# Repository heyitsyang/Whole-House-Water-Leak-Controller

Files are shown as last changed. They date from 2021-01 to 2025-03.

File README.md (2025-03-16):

# **Whole House Water Leak Detection & Valve Control**
The project described here is a part of a complete water detection system consisting of the following major components:
- Water Valve to cut off water flow should a leak be detected
- Pressure Sensor to detect small or slow leaks using a periodic static pressure test (weeping valves, toilet internals, etc.)
- Supervisory computer to schedule tests, analyze results, respond to leaks, and provide a UI.  I use Home Assistant, but a similar MQTT capable system should suffice.
- Remote water leak sensors placed under sinks and other areas of likely leakage to trigger immediate water cutoff for sudden leaks

The project detailed here satisfies the first two components in the list above.  A robust MQTT command set is incorporated for interfacing to a supervisory computer.

The code provided does not require the pressure sensor or the valve to be installed to be useful.  It is possible to use the system as a valve control box only or a pressure sensor only.
<br/><br/>
## **Pressure sensor**
If you need only valve control, the pressure sensor does not have to be installed. Just be sure to set the software accordingly either by setting the *#define INITIAL_PRESSURE_SENSOR_INSTALLED_STATE* directive in the code or during runtime using the *pressureInstalled* MQTT command.

The pressure sensor used is a M3200 series I2C interfaced model from TE Connectivity Industrial Pressure Sensors.  The specific model I used is M32JM-000105-100PG purchased from Mouser Electronics.  If you use this model be aware that external 4.7K pull up resistors are required for the SDA and SCL wires.

### **Pressure Sensor Default Programming**
Programming behavior can be changed by varying the *#define* directives in the program.  Here is the default behavior:
- Sensor is read every 500ms
- Under quiescent conditions, pressure is published every 5 minutes
- If there is a pressure change of more than 0.3 PSI, the current pressure is published every five seconds
- If the pressure sensor cannot be read a fault will be published every 5 minutes
<br/><br/>
## **Motorized Valve**
If you need only pressure sensing, the valve does not have to be installed.  Just be sure to set the software accordingly either by setting the *#define INITIAL_VALVE_INSTALLED_STATE* directive in the code or during runtime using the *valveInstalled* MQTT command.

The motorized valve used is a U.S. Solid model JFMSV00014 3/4" diameter Motorized Ball Valve (available on Amazon).  _Be sure you order the diameter approriate for your plumbing_.  

This model has five wires - two to control the valve (via polarity reversal) and three to connected to open/closed indicator switches.  There are other models from U.S. Solid that look the same but have different wire configurations.  The five-wire model is required if you wish to use this code without modification.

The five-wire model enables detection of the valve state.  Since there is a manual switch for opening/closing the valve, there is a possibilty that the last stored state of the valve in software is out of sync with the actual valve position.  The software compensates for this by sychronizing with the actual state of the valve.
<br/><br/>
## **Software**
The Water Main Controller software is written using PlatformIO.  However, it can be compiled using Arduino IDE by simply copying the text in src/main.cpp to a Arduino sketch file (e.g watermain.ino) and compiling using the IDE.  You will need to add the libraries indicated in the code comments before compiling.

### **Libraries**
Two libraries must be added to the development environment to sucessfully compile.  They are available via the Arduino or PlatformIO library manager or from github:
- knolleary/PuSubClient
- ropg/ezTime

### **MQTT**
All reporting and interaction with The Water Main Montior is accomplished via MQTT.  If you've never heard of MQTT, there are many good tutorials on the web,  It is best to have a firm grasp on MQTT concepts before beginning this project.

Although there is robust logging available from the serial port, the primary interface for interaction and configuration is through MQTT reports and commands.  The documentation for commands are in the code and are purposely not duplicated here to avoid having to maintain documentation in multiple places.

Using a MQTT tool such as MQTT Explorer (http://mqtt-explorer.com/) is strongly recommended to fully understand, configure, test, and debug the project.

### **Static Pressure Test**
Both the pressure sensor and the valve must be installed to use this feature.  

A Static Pressure Test is used to check for small leaks by turning off the water coming into the house for a short time and watching for a pressure drop when water is not being used and the hot water heater is not heating.  Determining hot water heater activity requires an additional sensor that is outside the scope of this project.  Short of sensing hot water heater activity, simply pick a time for the test when the hot water heater activity is unlikely.

The amount of pressure drop indicating a leak will vary with the plumbing system.  You will need to establish what pressure drop is normal for your properly sealed plumbing system in order to determine the setting for your leak alarm threshold.

A Static Pressure Test is initiated by sending the *sptStartTest* MQTT command (read code comments for all commands) to the controller.  Once the command is received, the test begins immediately.  

Results are published via MQTT at the end of the test.  It is up to program logic in the supervisory computer to determine if the test passed, failed, or is invalid due to water use or hot water heater activity.  In my case the program logic is accomplished using Home Assistant.
- Default SPT duration is 10 minutes
- Pressure reporting frequency is set to every 30 seconds during SPT.  Reporting frequency is restored to pre-test frequency when the test concludes.
- Valve is closed at the start and restored to pre-test state at end of test
- Timestamp of start of test, test duration, beginning pressure, ending pressure, and the difference is published via MQTT at the *end* of the test
- If a sudden/large pressure drop occurs during the SPT, the test a aborted, the valve is opened, and an aborted SPT status is published .  This avoids the inconvenience of water not being availble for the duration of the SPT test.  The supervisory computer can reschedule a test should this occur.

### **Home Assistant**
If you use Home Assistant, the following are the MQTT definitions required for your configuration.yaml.  You will need to study the MQTT commands and topics in the code to write your own data display, leak actions & alarms, etc.

Obviously, if you did not install both pressure sensor and valve, the Static Pressure Test and some parts of the MQTT configuration will not apply.

```
 mqtt:
    sensor:
      - unique_id: water_spt_data_status
        name: "SPT Data Status"
        state_topic: "watermain/spt_data_status"
        json_attributes_topic: "watermain/data_status/attributes"
        qos: 0

      - unique_id: water_pressure
        name: "Water Pressure"
        state_topic: "watermain/water_pressure"
        qos: 0
        device_class: "pressure"
        unit_of_measurement: "psi"
        expire_after: 600 # state becomes "unknown" after 10 minutes

      - unique_id: water_temperature
        name: "Water Temperature"
        state_topic: "watermain/water_temperature"
        qos: 0
        device_class: "temperature"
        unit_of_measurement: "°F"
        expire_after: 600 # state becomes "unknown" after 10 minutes

      - unique_id: unvalidated_water_static_pressure_test_result # see sensor.validated_water_static_pressure_test_result
        name: "Unvalidated Water Static Pressure Test Result"
        state_topic: "watermain/spt_result"
        unit_of_measurement: "psi"
        json_attributes_topic: "watermain/spt_result/attributes"

    switch:
      - name: "Water Valve"
        unique_id: water_valve
        state_topic: "watermain/valve_zeroisclosed"
        command_topic: "watermain/cmd/valveState"
        payload_on: "1"
        payload_off: "0"
        qos: 2
```
<br/>
The following are the template sensors derived from the the controller data.
<br/>

```
sensor:
    - platform: template
      sensors:
        last_static_pressure_test:
          friendly_name: "Last Static Pressure Test"
          value_template: >-
            {{ as_timestamp( state_attr('sensor.unvalidated_water_static_pressure_test_result', 'test_end'), '' ) 
            | timestamp_custom ('%m/%d %H:%M', True, 'unknown') }}

    - platform: template
      sensors:
        validated_water_static_pressure_test_result:
          friendly_name: "Validated Water Static Pressure Test Result"
          unit_of_measurement: "psi"
          value_template: >-
            {% if (is_state('sensor.spt_data_status', 'valid')) %}
              {{ states('sensor.unvalidated_water_static_pressure_test_result') }}
            {% endif %}

    - platform: template
      sensors:
        water_static_pressure_loss_per_minute:
          friendly_name: "Pressure Loss per Minute"
          unit_of_measurement: "psi"
          value_template: >
            {{ (states('sensor.validated_water_static_pressure_test_result') | float(default=0)) / 
              (states('input_number.inp_num_spt_duration') | float(default=0)) }}

    - platform: template
      sensors:
        min_water_pressure:
          friendly_name: "Min Water Pressure"
          unit_of_measurement: "psi"
          value_template: "{{ state_attr('sensor.24hr_avg_water_pressure', 'min_value') }}"

    - platform: template
      sensors:
        max_water_pressure:
          friendly_name: "Max Water Pressure"
          unit_of_measurement: "psi"
          value_template: "{{ state_attr('sensor.24hr_avg_water_pressure', 'max_value') }}"      
```
<br/>
To manually start the SPT test, use the following script.
<br/>

```
script:
  scr_manual_spt:
    sequence:
    - service: mqtt.publish
        data:
        topic: watermain/cmd/sptStart
```
For a more comprehensive example or more details, my complete Home Assistant code is available at https://github.com/yang3535/HomeAssistantConfigUnderHassOS.  Look in the following files and search for "spt" to see how I implemented various functions.
- automations/automations.yaml
- sensors.yaml
- scripts.yaml

<br/><br/>
Below is my Home Assistant dashboard for configuring & monitoring the system.  Note the water heater sensor shown in the dashboard is not part of this project.  Since the water heater being active influences the SPT results, I postpone the SPT test in my automation if the water heater is active.  If you run the Static Pressure Test in the middle of the night, water heater interference is less likely, so water heater sensor is optional.

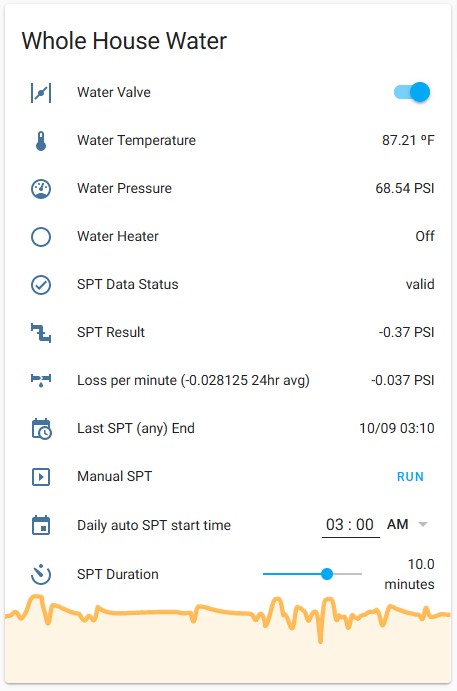
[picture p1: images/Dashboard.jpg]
Dashboard


<br/><br/>
## **Electronics**
The list of components I used is below.  It looks like a long list because of the URLs, but here are only eight main items.  If you plan to 3D print the enclosure, buying the specific electronic parts below will ensure fit inside the enclosure.

- Qty 1 - M32JM-000105-100PG - 
TE Connectivity Industrial Pressure Sensor part no. 20006465-00
 (Mouser Electronics part # 824-M32JM-000105-100) https://www.mouser.com/ProductDetail/Measurement-Specialties/M32JM-000105-100PG/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
- Qty 1 (optional)  - Motorized Ball Valve model JFMSV00014- .75" Stainless Steel Electrical Ball Valve with Full Port, 9-24V DC and 5 Wire Setup, can be used with Indicator Lights, [Indicate Open or Closed Position] by U.S. Solid
https://amazon.com/dp/B06Y11B8VN/ref=cm_sw_em_r_mt_dp_zI.YFbWGFTD1B?_encoding=UTF8&th=1
- Qty 1 - WeMos ESP8266 D1 Mini https://www.amazon.com/Makerfocus-NodeMcu-Development-ESP8266-Compatible/dp/B01N3P763C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
- Qty 1 - mxuteuk 3pcs/pkg (only one is needed) Momentary Rocker Switch Toggle Power Button (ON)/Off/(ON) 6 Pin 250V/10A 125V/15A, Use for Car Auto Boat Household Appliances KCD2-223-JT  by mxuteuk https://amazon.com/dp/B0885W19KL/ref=cm_sw_em_r_mt_dp_.A.YFbV7YQZZY?_encoding=UTF8&psc=1
- Qty 1 - Electronics-Salon 2 DPDT Signal Relay Module Board, DC 5V Version, for Arduino Raspberry-Pi 8051 PIC.  by Electronics-Salon.  https://www.amazon.com/Electronics-Salon-Signal-Version-Arduino-Raspberry-Pi/dp/B00SKG6OM4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
- Qty 1 - RGB LED https://www.amazon.com/Diffused-Multicolor-Common-Cathode-Arduino/dp/B01FDD3B72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
- Qty 1 - LM2596 Buck Converter https://www.amazon.com/DZS-Elec-Adjustable-Electronic-Stabilizer/dp/B06XRN7NFQ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
- Qty 1 - 12VDC Power supply 
https://amazon.com/gp/product/B07HNV6SBJ/ref=ppx_yo_dt_b_asin_title_o01_s00?ie=UTF8&psc=1

The panel mount holes of the 3D printed enclosure accomodates the specific connectors listed below.  If you don't want to use these connectors, the 3D Fusion360 source file can be modified to suit whatever connectors you choose.

Note the aviation connectors below are specified with different number of pins to prevent accidentally interchanging the pressure sensor and the valve control wires.  It is possible to use the 6-pin version for both wires if you don't confuse the two or select pin connections so no harm is done if interchanged.  

- Qty 1 - Female DC Power Jack Panel Mount 5.5mm x 2.1mm https://www.amazon.com/TOTOT-5-5mm-Female-Socket-Electrical/dp/B077YB75N3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
- Qty 1 - 4-pin Aviation Connector set https://amazon.com/gp/product/B07GZFQDNS/ref=ppx_yo_dt_b_search_asin_title?ie=UTF8&psc=1
- Qty 1 - 6-pin Aviation Connector set https://smile.amazon.com/gp/product/B07L1Q69R5/ref=ppx_yo_dt_b_search_asin_title?ie=UTF8&psc=1
<br/><br/>
### Wiring & Assembly

Wiring Diagram - The Wemos D1 Mini ESP8266 device is shown right side up in the diagram below for clarity, but will actually be mounted upside down in the 3D printed enclosure.

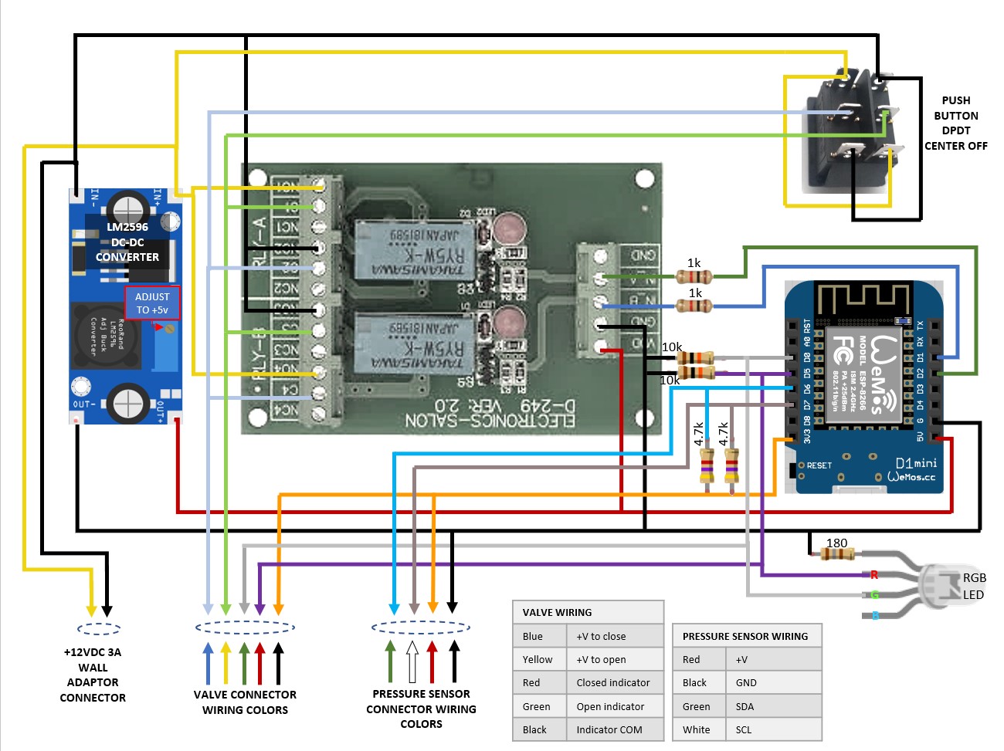
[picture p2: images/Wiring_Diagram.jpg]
Circuit Diagram

<br/><br/> 

Components mounted in 3D printed case - Note the color of wires do not match those of the above diagram.  The indicator LED is mounted above the manual valve control on the right side.  The leftmost aviation connector is  currently unused.

Components
<br/><br/> 

Installed project - Leftmost avaition connector is currently unused.  The blue cylinders are a whole-house water filter which conveniently had a 1/4" NPT fitting suitable for the pressure sensor.

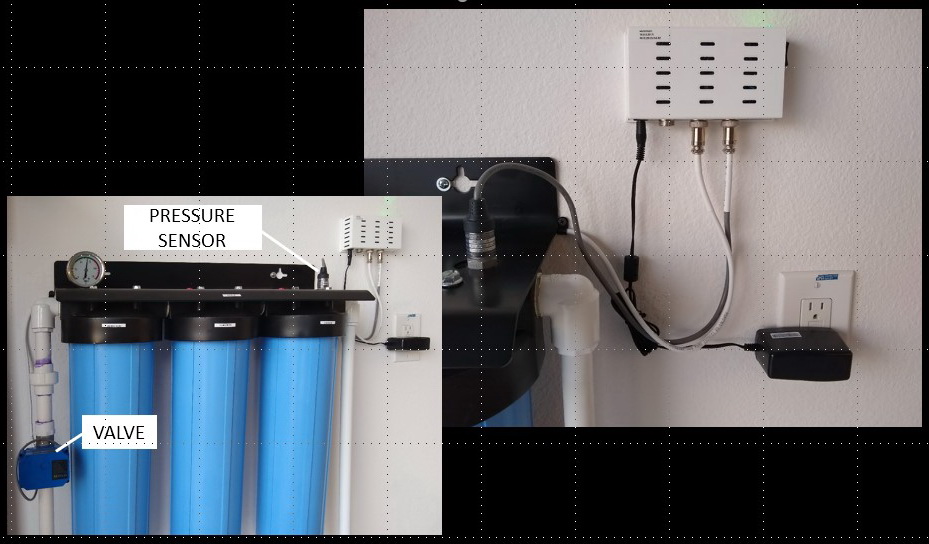
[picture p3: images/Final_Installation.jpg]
Complete

<br/><br/>
## **3D Printed Enclosure**
3D Printing files and the Fusion360 source file are available in this repository under the 3D_Printed_Enclosure directory.  I printed my enclosure using PETG to avoid potential shrinkage issues surrounding the snap-on lid, but there is nothing special about PETG otherwise.  Both STL and Fusion360 files are provided.  If you don't have a 3D printer, there are many services available online that will print for a fee.

You will need to print the bottom, the lid, and one of the two slide-in mounts depending on desired final orientation.

- The wiring diagram above shows the WeMos ESP8266 D1 Mini ESP8266 board right side up for clarity, but it is mounted upside-down in the enclosure for assembly.  Be aware of this before you start wiring.

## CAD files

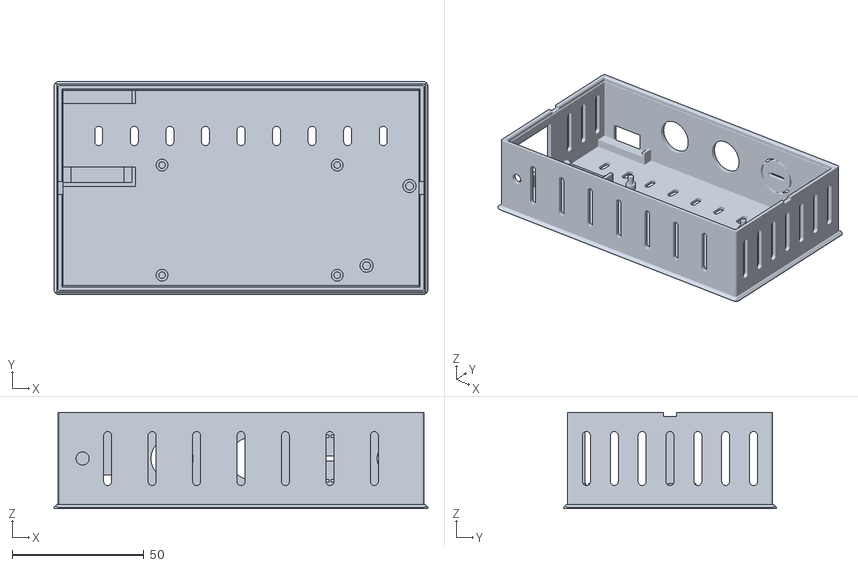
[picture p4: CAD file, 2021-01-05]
3D_Printed_Enclosure/Enclosure bottom.stl
142.0 x 81.0 x 36.5

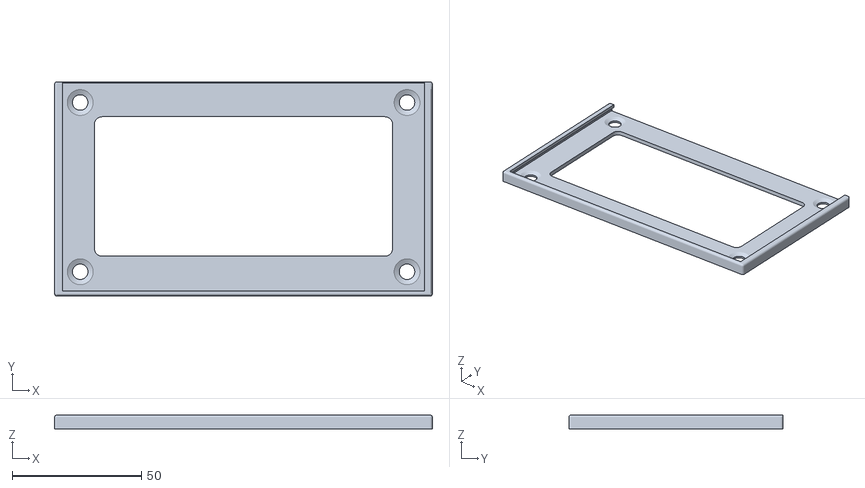
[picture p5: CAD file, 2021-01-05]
3D_Printed_Enclosure/Vertical slide-in mount.stl
146.3 x 82.9 x 5.45

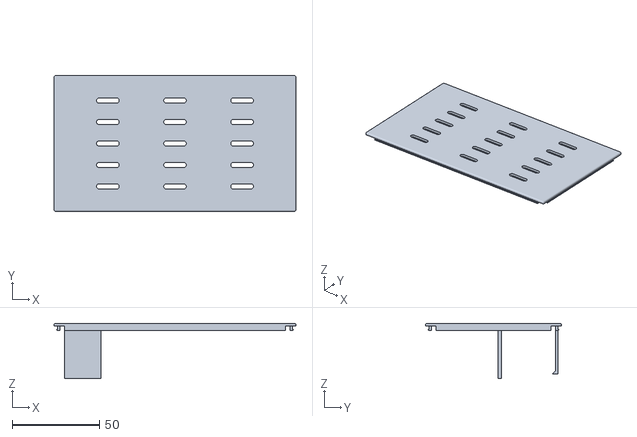
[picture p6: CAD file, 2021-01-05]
3D_Printed_Enclosure/Enclosure lid.stl
139.0 x 78.0 x 31.8

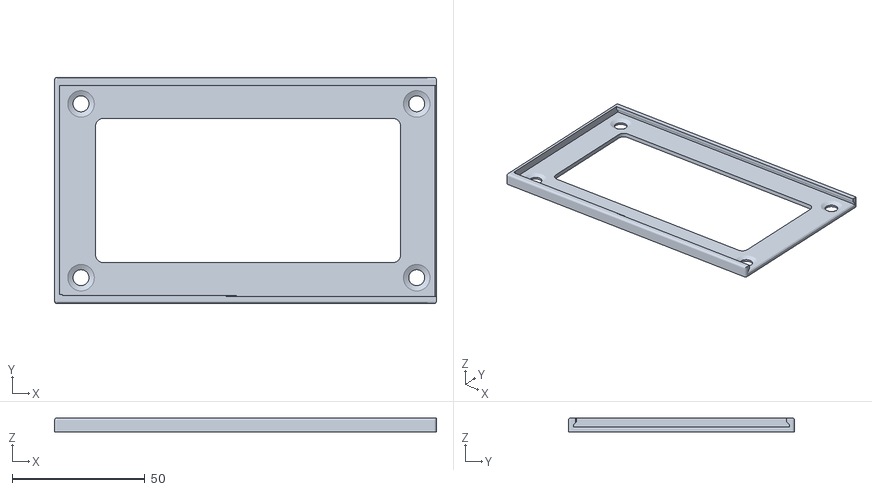
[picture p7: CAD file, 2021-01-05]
3D_Printed_Enclosure/Horizontal slide-in mount.stl
143.9 x 85.3 x 5.45

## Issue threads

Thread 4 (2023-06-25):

Feature request: Watermeter HomeWizard support

liudger, 2023-06-25:
https://www.homewizard.com/watermeter/ is a watermeter that just is metering the water throughput. Is this something that could switched with the pressure detection?

heyitsyang, 2023-06-25:
A valve is required to switch the water on/off.  There is no valve in the meter in the link you provided, so there is nothing to switch.

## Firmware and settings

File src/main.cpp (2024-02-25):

#include <ESP8266WiFi.h>
#include <ESP8266mDNS.h>
#include <WiFiUdp.h>
#include <LittleFS.h>
#include <ArduinoOTA.h>
#include <Wire.h>
// add the below libraries from the Library Manager
#include <PubSubClient.h>
#include <ezTime.h>

// private definitions
#include "private.h"               // <<<<<<<  COMMENT THIS OUT FOR YOUR INSTANCE - this contains stuff for my WIFI network, not yours

#define VERSION "Ver 3.2 build 2024-02-25"

// i2c pins are usually D1 & D2, but this application requires use of D1 & D2, so
// D6 & D7 are used instead - see Valve Control Settings below for explanation
#define I2C_ADDR 0x28
#define MAX_PRESSURE 100
#define PIN_SDA D6 // (GPIO12)  Pins where i2c
#define PIN_SCL D7 // (GPIO13)  SDA & SDL are attached

// Valve control settings
// On the ESP8266 pins D1 & D2 are the only two GPIOs that do not glitch HIGH at startup/reset.
// Since the valve relay wiring cannot tolerate the glitch (will short the power), we must use D1 & D2 here.
#define PIN_VALVE_ON D1                // (GPIO5)   Valve works by reversing voltage on a set of two wires
#define PIN_VALVE_OFF D2               // (GPIO4)   DO NOT SET VALVE_ON & VALVE_OFF high at the same time!! It will short out the power supply!!
#define PIN_VALVE_ON_INDICATOR D0      // (GPIO16)  Confirms valve is in ON position when signal high
#define PIN_VALVE_OFF_INDICATOR D5     // (GPIO14)  Confirms valve is in OFF position when signal high

// Flow meter
#define PIN_FLOW_SIGNAL D8             // (GPIO15) Unimplemented

// Name your device here
#define DEVICE_NAME "watermain"

#ifndef WIFI_SSID
#define WIFI_SSID "your_ssid"            //  <<<<<<<  REPLACE WITH YOUR CREDENTIALS
#endif
#ifndef WIFI_PASSWORD
#define WIFI_PASSWORD "your_password"    //  <<<<<<<  REPLACE WITH YOUR CREDENTIALS
#endif

// Time settings
#define MY_TIMEZONE "America/New_York"               // <<<<<<< use Olson format: https://en.wikipedia.org/wiki/List_of_tz_database_time_zones

// MQTT
#define MQTT_USER_NAME "watermain"                   // <<<<<<< replace with your MQTT login
#define MQTT_PASSWORD "watermain"                    // <<<<<<< replace with your MQTT password
#define MQTT_SERVER "haha.shencentral.net"           // <<<<<<< use either your MQTT broker DNS name or IP address surrounded by quotes

#define MSG_BUFFER_SIZE 512                          // for MQTT message payload
#define VERSION_TOPIC "watermain/report/version"     // report software version at connect
#define LAST_BOOT_TOPIC "watermain/report/last_boot" // send boot (not reconnect) time to broker when connected
#define LWT_TOPIC "watermain/status/LWT"             // MQTT Last Will & Testament
#define REPORT_TOPIC "watermain/report/params"       // used to send program operating parameters
#define HELP_TOPIC "watermain/report/help"           // used to send program operating info
#define PRESSURE_TOPIC "watermain/water_pressure"
#define TEMPERATURE_TOPIC "watermain/water_temperature"
#define PRESSURE_SENSOR_FAULT_TOPIC "watermain/report/last_press_sensor_fault" // sends timestamp if pressure error can't be read
#define VALVE_TOPIC "watermain/valve_zeroisclosed"                             // valve position 0 = closed, 1= open
#define LAST_VALVE_STATE_UNK_TOPIC "watermain/report/last_unk_valve_state"     // send timestamp if valve state cannot be determined from indicator inputs
#define SPT_DATA_STATUS_TOPIC "watermain/spt_data_status"                      // 0 when test in progress, 1 when finished
#define SPT_RESULT_TOPIC "watermain/spt_result"                                // send at end of Static Pressure Test - end pressure minus start pressure
#define RECV_COMMAND_TOPIC "watermain/cmd/#"

// Operational parameters & preferences
#define PREFER_FAHRENHEIT 1                          // temperature reported in Celsius unless this is set to 1
#define INITIAL_VALVE_INSTALLED_STATE 1              // 1 if installed, 0 if not - runtime state can be changed & saved in NVRAM via MQTT command
#define INITIAL_PRESSURE_SENSOR_INSTALLED_STATE 1    // 1 if installed, 0 if not - runtime state can be changed & saved in NVRAM via MQTT command
#define PARAMS_FILENAME "/params.bin"
#define VALVE_STATE_FILENAME "/valve_state.bin"
#define OPEN_VALVE 1
#define CLOSE_VALVE 0
#define PRESSURE_SETTLING_DELAY_MS 2000              // wait for pressure to settle a bit after closing valve for SPT
#define VALVE_ROTATION_TIME_MS 10000                 // time required for valve to open/close - relays are only active long enough for the valve to rotate
#define VALVE_ERROR_DEFAULT 0                        // 0=CLOSED, 1=OPEN - how the valve will default if everything goes badly - also used if manual switch has left valve between OPEN/CLOSED
#define VALVE_SYNC_INTERVAL_MS 30000                 // how often actual valve switch will be checked & synced with software valveState (in case manual button has been used)
#define DEFAULT_IDLE_PUBLISH_INTERVAL_MS 300000      // how often sensor data is published if no event driven changes
#define DEFAULT_MIN_PUBLISH_INTERVAL_MS 5000         // don't publish more often than this in non-SPT operation
#define SPT_MIN_PUBLISH_INTERVAL_MS 1000             // don't publish more often than this during SPT
#define PRESSURE_SENSOR_FAULT_PUB_INTERVAL_MS 60000  // how often a pressure sensor error (timestmap) is published if error condition true
#define DEFAULT_SENSOR_READ_INTERVAL_MS 500          // how often the sensor is read (how soon PSI changes are recognized)
#define DEFAULT_SPT_REPORT_PSI_DROP .3               // amount of change in PSI to initiate a publishing event
#define DEFAULT_SPT_DEMAND_WATER_PERCENT_DROP 30     // percent of sudden pressure drop during Static Pressure Test required to assume pressure drop is intentional (water is needed)
#define DEFAULT_SPT_TEST_DURATION_MINUTES 10         // duration of Static Pressure Test (valve off & observe pressure change)
#define SPT_DATA_IN_PROCESS "in_process"             // SPT test is in process and the reported SPT result is old
#define SPT_DATA_VALID "valid"                       // SPT test has completed normally and the SPT result is valid
#define SPT_DATA_ABORTED "aborted"                   // SPT test has terminated abnormally and resultant data is not valid (test must be run again)
#define SPT_DATA_INVALID "not_valid"                 // SPT test has not been run

#define TIMEZONE_EEPROM_OFFSET 0                     // location-to-timezone info - saved in case eztime server is down

#define DEBUG_SPT false                               // Disable valve synce for testing <<<<<  DON'T FORGET TO CHANGE THIS BACK TO false AFTER TESTING <<<<<<<<<<<<<

char msg[MSG_BUFFER_SIZE];
char lastBoot[50];
unsigned long lastReconnectAttempt = 0;
unsigned long lastPublish = 0, lastRead = 0, lastValveSync = 0, lastPressErrReport = 0;
unsigned long tempNow, lastPublishNow, sensorReadNow, mqttNow, valveNow, lastValveSyncNow, lastPressErrReportNow;
byte sensorStatus;
float psiTminus0 = 0, psiTminus1 = 0, psiTminus2 = 0;            // psiTminus0 is the current pressure, psiTminus1 is the previous, psiTminus2 is the one before
float medianPressure, sptBeginningPressure, temperature;
unsigned int pre_spt_idlePublishInterval, pre_spt_minPublishInterval;

struct Parameters
{
  char version[30];
  unsigned int valveInstalled;
  unsigned int pressureInstalled;
  unsigned int idlePublishInterval;
  unsigned int minPublishInterval;
  unsigned int sensorReadInterval;
  float sptPressureDrop;
  float sptDemandWaterPercentDrop;
  unsigned int sptDuration;
  byte filler;  // NVM requires even number of bytes for storage
};

struct Parameters opParams;

byte valvePreSPT, valveState = VALVE_ERROR_DEFAULT; // if all saved data is lost, VALVE_ERROR_DEFAULT is the valve setting
unsigned int sptConsecAborts = 0;
char sptDataStatus[12];
File paramFileObj, valveFileObj;
WiFiClient espClient;
PubSubClient mqttClient(espClient);
Timezone myTZ;

//   ***************************
//   **  WiFi initialization  **
//   ***************************

void setup_wifi()
{
  delay(10); // let Serial comm stream start before using it

  // We start by connecting to a WiFi network

  WiFi.mode(WIFI_STA);
  WiFi.setHostname(DEVICE_NAME);
  WiFi.begin(WIFI_SSID, WIFI_PASSWORD);

  Serial.print(F("\nWaiting for WiFi "));
  while (WiFi.status() != WL_CONNECTED)
  {
    Serial.print(F("."));
    delay(500);
  }

  randomSeed(micros());

  Serial.println(F(""));
  Serial.print(F("WiFi connected to "));
  Serial.println(WIFI_SSID);
  Serial.print(F("IP address: "));
  Serial.println(WiFi.localIP());
}

//   ************************
//   ** OTA initialization **
//   ************************

void setup_OTA()
{
  // Port defaults to 8266
  // ArduinoOTA.setPort(8266);

  // Hostname defaults to esp8266-[ChipID]
  // ArduinoOTA.setHostname(DEVICE_NAME);

  // No authentication by default
  // ArduinoOTA.setPassword("admin");

  // Password can be set with it's md5 value as well
  // MD5(admin) = 21232f297a57a5a743894a0e4a801fc3
  // ArduinoOTA.setPasswordHash("21232f297a57a5a743894a0e4a801fc3");

  ArduinoOTA.onStart([]() {
    String type;
    if (ArduinoOTA.getCommand() == U_FLASH)
    {
      type = "sketch";
    }
    else
    { // U_FS
      type = "filesystem";
    }

    // NOTE: if updating FS this would be the place to unmount FS using FS.end()
    paramFileObj.close();
    valveFileObj.close();
    LittleFS.end();          //  <<<<<< This line required to prevent FS damage
    mqttClient.disconnect(); // let broker know it is expected

    Serial.println("Start updating " + type);
  });
  ArduinoOTA.onEnd([]() {
    Serial.println(F("\nEnd"));
  });
  ArduinoOTA.onProgress([](unsigned int progress, unsigned int total) {
    Serial.printf("Progress: %u%%\r", (progress / (total / 100)));
  });
  ArduinoOTA.onError([](ota_error_t error) {
    Serial.printf("Error[%u]: ", error);
    if (error == OTA_AUTH_ERROR)
    {
      Serial.println(F("Auth Failed"));
    }
    else if (error == OTA_BEGIN_ERROR)
    {
      Serial.println(F("Begin Failed"));
    }
    else if (error == OTA_CONNECT_ERROR)
    {
      Serial.println(F("Connect Failed"));
    }
    else if (error == OTA_RECEIVE_ERROR)
    {
      Serial.println(F("Receive Failed"));
    }
    else if (error == OTA_END_ERROR)
    {
      Serial.println(F("End Failed"));
    }
  });
  ArduinoOTA.begin();
}

//   *************************
//   **  applyValveState()  **
//   *************************

// 0 = closed 1 = open
boolean applyValveState(int desiredState, boolean writeFlag) // this routine uses the global char msg[], it does not set valveState global
{
  char val[3];
  switch (desiredState)
  {
  case 0:
    digitalWrite(PIN_VALVE_OFF, HIGH);                       // turn on just enough to rotate valve
    Serial.print(F("Closing valve..."));
    valveNow = millis();
    while (millis() - valveNow < VALVE_ROTATION_TIME_MS)
      yield();
    digitalWrite(PIN_VALVE_OFF, LOW);
    Serial.println(F("valve is CLOSED (state=0)"));
    sprintf(val, "%d", desiredState);
    mqttClient.publish(VALVE_TOPIC, val, true);
    Serial.printf("%s MQTT SENT: %s/%s \n", myTZ.dateTime("[H:i:s.v]").c_str(), VALVE_TOPIC, val);

    if (writeFlag == true)
    {
      valveFileObj = LittleFS.open(F(VALVE_STATE_FILENAME), "r+");
      if (valveFileObj.write((uint8_t *)&desiredState, sizeof(desiredState)) > 0)
        Serial.println(F("Valve state saved"));
      else
        Serial.println(F("Valve file update error"));
      valveFileObj.close();
    }
    return (true);
    break;
  case 1:
    digitalWrite(PIN_VALVE_ON, HIGH);                        // turn on just enough to rotate valve
    Serial.print(F("Opening valve..."));
    valveNow = millis();
    while (millis() - valveNow < VALVE_ROTATION_TIME_MS)
      yield();
    digitalWrite(PIN_VALVE_ON, LOW);
    Serial.println(F("valve is OPEN (state=1)"));
    sprintf(val, "%d", desiredState);
    mqttClient.publish(VALVE_TOPIC, val, true);
    Serial.printf("%s MQTT SENT: %s/%s \n", myTZ.dateTime("[H:i:s.v]").c_str(), VALVE_TOPIC, val);

    if (writeFlag == true)
    {
      valveFileObj = LittleFS.open(F(VALVE_STATE_FILENAME), "r+");
      if (valveFileObj.write((uint8_t *)&desiredState, sizeof(desiredState)) > 0)
        Serial.println(F("Valve state saved"));
      else
        Serial.println(F("Valve file update error"));
      valveFileObj.close();
    }
    return (true);
    break;
  default:
    Serial.println(F("Invalid valveState requested"));
    return (false);
  }
}
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
void loop()
{

  ArduinoOTA.handle();
  events(); // exececute ezTime events i.e. Static Pressure Test

  if (!mqttClient.connected())
  {
    mqttNow = millis();
    if (mqttNow - lastReconnectAttempt > 1000)
    {
      Serial.printf("[%s] Waiting for MQTT...\n", myTZ.dateTime(RFC3339).c_str());
      lastReconnectAttempt = mqttNow;
      // Attempt to reconnect
      if (reconnect())
      {
        lastReconnectAttempt = 0;
      }
    }
  }
  else
  {
    // Client connected
    mqttClient.loop();
  }

  // Sync valve state
  if ( (opParams.valveInstalled == 1) && (!DEBUG_SPT) )
  {
    // Periodically check to sync software valveState with actual indicator inputs in case manual valve switch was used
    //  - this polling method used because manual override may result in half on/off state for an unknown amount of time
    lastValveSyncNow = millis();
    if ((unsigned long)(lastValveSyncNow - lastValveSync) > (unsigned long)VALVE_SYNC_INTERVAL_MS)
    {
      if ((digitalRead(PIN_VALVE_ON_INDICATOR) == LOW) && (digitalRead(PIN_VALVE_OFF_INDICATOR) == LOW)) // valve left half open/closed
      {
        Serial.println(F("Actual valve state cannot be determined.  Setting valve to defined VALVE_ERROR_DEFAULT"));
        mqttClient.publish(LAST_VALVE_STATE_UNK_TOPIC, myTZ.dateTime(RFC3339).c_str(), true);
        Serial.printf("%s MQTT SENT: %s/%s \n", myTZ.dateTime("[H:i:s.v]").c_str(), LAST_VALVE_STATE_UNK_TOPIC, myTZ.dateTime(RFC3339).c_str());
        valveState = VALVE_ERROR_DEFAULT;
        applyValveState(VALVE_ERROR_DEFAULT, false); // this can be a loop if valve is half open/closed, so do not write to flash
        Serial.println(F("To protect flash memory, valveState not saved"));
      }
      else
      {
        if ((digitalRead(PIN_VALVE_ON_INDICATOR) == HIGH) && (valveState != 1))
        {
          Serial.println(F("valveState CONFLICT DETECTED - syncing to actual: valveState=1"));
          valveState = 1;
          applyValveState(valveState, true);
        }
        if ((digitalRead(PIN_VALVE_OFF_INDICATOR) == HIGH) && (valveState != 0))
        {
          Serial.println(F("valveState CONFLICT DETECTED - syncing to actual: valveState=0"));
          valveState = 0;
          applyValveState(valveState, true);
        }
      }
      lastValveSync = millis();
    }
  }

  // Sanity check to prevent MQTT flooding - reset ALL to defaults if parameters seem corrupted
  if ((opParams.idlePublishInterval < DEFAULT_MIN_PUBLISH_INTERVAL_MS) || (opParams.minPublishInterval < DEFAULT_SENSOR_READ_INTERVAL_MS) 
       || (opParams.sensorReadInterval < 3) || (opParams.sptPressureDrop <= (float).2) || (opParams.sptDuration < 1))
  {
    Serial.printf("Parameters loaded from file %s \n", PARAMS_FILENAME);
    Serial.printf("{\"version\": \"%s\", \"valveInstalled\": \"%d\", \"pressureInstalled\": \"%d\", \"idlePublishInterval\": \"%d\", "
                  "\"minPublishInterval\": \"%d\", \"sensorReadInterval\": \"%d\", \"sptPressureDrop\": \"%.2f\", \"sptDemandWaterPercentDrop\": \"%.f\", \"sptDuration\": \"%d\"}\n\n",
                  opParams.version, opParams.valveInstalled, opParams.pressureInstalled, opParams.idlePublishInterval, opParams.minPublishInterval,
                  opParams.sensorReadInterval, opParams.sptPressureDrop, opParams.sptDemandWaterPercentDrop, opParams.sptDuration);
    strcpy(opParams.version, VERSION);
    opParams.valveInstalled = INITIAL_VALVE_INSTALLED_STATE;
    opParams.pressureInstalled = INITIAL_PRESSURE_SENSOR_INSTALLED_STATE;
    opParams.idlePublishInterval = DEFAULT_IDLE_PUBLISH_INTERVAL_MS;
    opParams.minPublishInterval = DEFAULT_MIN_PUBLISH_INTERVAL_MS;
    opParams.sensorReadInterval = DEFAULT_SENSOR_READ_INTERVAL_MS;
    opParams.sptPressureDrop = (float)DEFAULT_SPT_REPORT_PSI_DROP;
    opParams.sptDemandWaterPercentDrop = (float)DEFAULT_SPT_DEMAND_WATER_PERCENT_DROP;
    opParams.sptDuration = DEFAULT_SPT_TEST_DURATION_MINUTES;
    Serial.println(F("PARAMETER SANITY CHECK FAILED.  All parameters reset to defaults. "));
    paramFileObj = LittleFS.open(F(PARAMS_FILENAME), "w+");
    if (paramFileObj.write((uint8_t *)&opParams, sizeof(opParams)) > 0)
      Serial.printf("New parameters file created: %s, %d bytes\n", paramFileObj.name(), paramFileObj.size());
    else
      Serial.println(F("Parameters file creation error"));
    paramFileObj.close();
  }


  // Read sensor
  if (opParams.pressureInstalled == 1)
  {
    sensorStatus = 0xFF; // set to non-zero for initial while() test
    sensorReadNow = millis();
    if ((unsigned long)(sensorReadNow - lastRead) > opParams.sensorReadInterval)
    {
      lastRead = millis();
      while (sensorStatus != 0) // continue reading until valid
      {
        Wire.requestFrom(I2C_ADDR, 4); // request 4 bytes  - if optional 3rd argument false = don't share i2c bus
        int n = Wire.available();
        if (n == 4)
        {
          sensorStatus = 0;  // set to zero to exit while loop when read is successful
          uint16_t rawP; // pressure data from sensor
          uint16_t rawT; // temperature data from sensor

          rawP = (uint16_t)Wire.read(); // upper 8 bits
          rawP <<= 8;
          rawP |= (uint16_t)Wire.read(); // lower 8 bits
          rawT = (uint16_t)Wire.read();  // upper 8 bits
          rawT <<= 8;
          rawT |= (uint16_t)Wire.read(); // lower 8 bits

          sensorStatus = rawP >> 14; // The status is 0, 1, 2 or 3
          rawP &= 0x3FFF;            // keep 14 bits, remove status bits

          rawT >>= 5; // the lowest 5 bits are not used

          psiTminus0 = ((rawP - 1000.0) / (15000.0 - 1000.0)) * MAX_PRESSURE;
          temperature = ((rawT - 512.0) / (1075.0 - 512.0)) * 55.0;
        }
        else
        {
          lastPressErrReportNow = millis();
          if ((unsigned long)(lastPressErrReportNow - lastPressErrReport) > (unsigned long)PRESSURE_SENSOR_FAULT_PUB_INTERVAL_MS)
          {
            Serial.println(F("Error reading pressure sensor"));
            mqttClient.publish(PRESSURE_SENSOR_FAULT_TOPIC, myTZ.dateTime(RFC3339).c_str(), true);
            Serial.printf("%s MQTT SENT: %s/%s \n", myTZ.dateTime("[H:i:s.v]").c_str(), PRESSURE_SENSOR_FAULT_TOPIC, myTZ.dateTime(RFC3339).c_str());
            lastPressErrReport = millis();
          }
          while ((millis() - lastPressErrReportNow) < opParams.sensorReadInterval); // prevent cycling too fast
          break;
        }
      }
    }

    lastPublishNow = millis();
    if (  ( ((unsigned long)(lastPublishNow - lastPublish) > opParams.idlePublishInterval) ||
        ((fabs(psiTminus1 - psiTminus0) > opParams.sptPressureDrop) && (lastPublishNow - lastPublish >= opParams.minPublishInterval)) ) &&
        mqttClient.connected()  )
    {
      // use MEDIAN of last three readings to filter glitches - psiTminus0 is latest reading, psiTminus2 is oldest
      // MEDIAN is the middle of the last three readings - not the average
      if ((psiTminus1 != 0) && (psiTminus2 != 0))
      {
        if ((psiTminus1 > psiTminus2 && psiTminus2 > psiTminus0) || (psiTminus0 > psiTminus2 && psiTminus2 > psiTminus1))
          medianPressure = psiTminus2;
        if ((psiTminus2 > psiTminus1 && psiTminus1 > psiTminus0) || (psiTminus0 > psiTminus1 && psiTminus1 > psiTminus2))
          medianPressure = psiTminus1;
        if ((psiTminus2 > psiTminus0 && psiTminus0 > psiTminus1) || (psiTminus1 > psiTminus0 && psiTminus0 > psiTminus2))
          medianPressure = psiTminus0;
      }
      else
      {
        medianPressure = psiTminus0;
      }
      sprintf(msg, "%.2f", medianPressure);
      mqttClient.publish(PRESSURE_TOPIC, msg);
      Serial.printf("\n%s MQTT SENT: %s/%s \n", myTZ.dateTime("[H:i:s.v]").c_str(), PRESSURE_TOPIC, msg);
      if (PREFER_FAHRENHEIT == 1)
        temperature = (1.8 * temperature + 32);
      sprintf(msg, "%.2f", temperature);
      mqttClient.publish(TEMPERATURE_TOPIC, msg);
      Serial.printf("%s MQTT SENT: %s/%s \n", myTZ.dateTime("[H:i:s.v]").c_str(), TEMPERATURE_TOPIC, msg);
      lastPublish = millis();
      psiTminus2 = psiTminus1; // rotate queue
      psiTminus1 = psiTminus0;
    }
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

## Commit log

2020-12-26 Add Static PressureTest (SPT) function
2021-01-04 Valve integration changes
2021-01-16 DIrectory rename
    [Enclosure bottom.stl, Enclosure lid.stl, Horizontal slide-in mount.stl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]
2021-01-16 add pressureInstalled flag & logic
2021-01-27 change pressure reporting frequency during SPT
2021-01-29 Add detection for valveState violation during SPT
2021-02-17 delay to slow reading of pressure sensor if error
    [main.cpp]
2021-02-18 change pressure sensor fault reporting interval
2021-02-19 add Wire.available() call
2021-03-09 don't zero pressure and temperature as faults
2021-03-09 tweak pressure sensor read loop
2021-03-17 change SPT pressure read interval
2021-03-25 Shorten activity publish interval during SPT
    [main.cpp]
2021-06-29 Added valve reversal on water demand during SPT
    [main.cpp]
2021-08-22 Fix bypass of test_end & attr when aborted
    [main.cpp]
2023-02-15 Fixed wire color alignment for valve connection
2023-02-16 fix missing relay output black wire
2023-02-27 add resistors
2024-02-25 fix setting of hostname
    [main.cpp]
